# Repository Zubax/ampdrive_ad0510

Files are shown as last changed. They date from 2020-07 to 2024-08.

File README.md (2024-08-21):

# AmpDrive AD0510 / Zubax Komar

Zubax Komar is a high-quality FOC ESC based on [Telega](https://zubax.com/technologies/telega) motor control technology.
Komar is designed to support the propulsion systems of light unmanned aerial vehicles (UAVs), unmanned underwater vehicles (UUVs)
and unmanned surface vehicles (USVs). Komar is compatible with almost all PMSM and BLDC motors.
It is designed to be a part of an integrated drive but allows operation as a separate unit as well.
Komar is one of the reference designs for the [Mitochondrik LV](https://zubax.com/products/mitochondrik-lv) control module.

<p align="center">
Zubax Komar
</p>

## Brief specs

* 12...51 V input voltage range (4...12S LiCoO<sub>2</sub> battery).
* Up to 2500 W output power (with 12S LiCoO<sub>2</sub> battery).
* Maximum continuous phase current amplitude 100 A.
* A software-controllable 5 V BEC.
* Built-in motor temperature sensor for enhanced self-diagnostics.
* Komar supports a rich set of communication interfaces:
  * Double redundant CAN bus interface.
  * USB Micro-B interface for control, management, and telemetry.
  * Industry-standard RC PWM input.
* Komar is built using highly reliable automotive-grade AEC-Q qualified components.
* Operating device temperature - -40..85 °C.
* Operating humidity - 0..100 %RH (Condensation not permitted).
* Weight - 96.5 g (cables not included).

Due to its superb efficiency, Komar can operate at high power levels using only a very lightweight and compact heatsink to cool the device down.

Komar is designed to be a part of an integrated drive for mid-power motors.
It is best suited for motors with the following specs:

* Continuous power: 2.5 kW
* Continuous phase current amplitude: 90 A
* Outer diameter: 80 mm

Komar can also be used as a separate unit. In this case, a custom phase connector mounted on the housing may be used to provide motor connections.

The parameters of the Aux port are as follows:

* $V_\text{pull}=3.3V$ (defined by Mitochondrik)
* $R_\text{pull}=1200\Omega$ (defined by Mitochondrik)
* $R_\text{io}=200\Omega$ at the Aux connector
* $R_\text{io}=0\Omega$ at the through-hole motor thermistor pin on the PCB (see schematics)

## Construction and usage

Komar itself consists of a power stage PCB with Mitochondrik and the housing (aluminum enclosure plus several plastic parts).
The PCB may use several optional 3D-printed parts that don't influence its properties directly, but may improve the overall user experience:

- Lightpipe
- Capacitor support

## Connections and indication

All connections (except the phase connector) and indicators are presented on the bottom cover, as shown in figure below.

Komar connectors and LEDs placement

Pinout of connectors is presented in the tables below. 

### CAN1 & CAN2 connectors (type JST BM04B-GHS)

| Pin # | Type  | Name  | Comments |
|---|---|---|---|
| 1 | Power | PWR | BEC 5V power output. Activated in the firmware. |
| 2 | I/O | CAN_H | |
| 3 | I/O | CAN_L | |
| 4 | Power | GND | |

The device does not terminate the CAN bus internally.
If the bus is not redundant, only CAN1 (the primary CAN bus interface) can be used.

### AUX connector (type JST BM04B-GHS)

| Pin # | Type  | Name  | Comments |
|---|---|---|---|
| 1 | Power | PWR | 5V line output |
| 2 | I/O | GPIO1 | GPIO/RCPWM input/Thermistor input |
| 3 | I/O | GPIO2 | |
| 4 | Power | GND | |

The motor windings temperature can be measured by means of a PTC thermistor. The following thermistors can be connected between GPIO1 and GND:

- KTY84/130
- KTY81/120
- KTY83/120

No additional components are needed for the thermistor. The thermistor model is selected in the firmware.

### USB connector

Common USB 2.0 Micro-USB connector is dedicated for the device configuration and control using the [Kucher GUI](https://files.zubax.com/products/com.zubax.kucher/1.0.0/).

## Thermal performance

Thermal simulation is performed under the following conditions:

* The heat source is applied to the heatsink area where the PCB is placed. Its power is 78.5 W.
  It is a typical value of power losses in the Komar power stage when operating at a power level of 2500 W
  and powered from a discharged 12S battery (~40 V). This should represent the worst-case scenario.

* Ambient temperature is 20 °C.

* The convection value of 350 W/(m<sup>2</sup>K) is established empirically after conducting several experiments with real hardware.

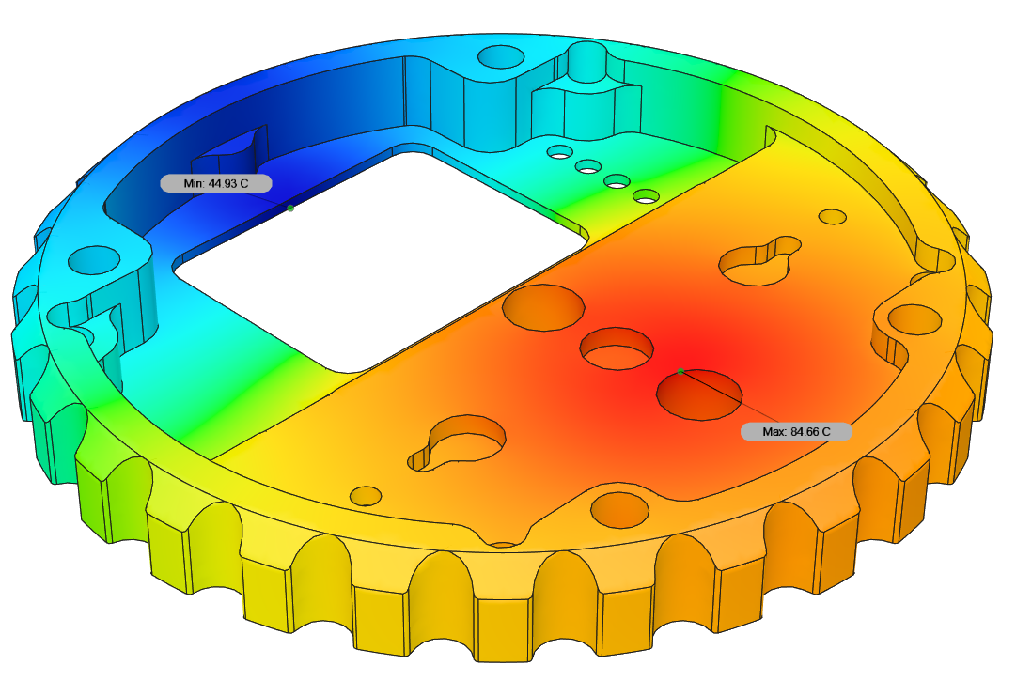
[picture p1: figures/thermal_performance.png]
Zubax Komar thermal performance


## Mounting pattern

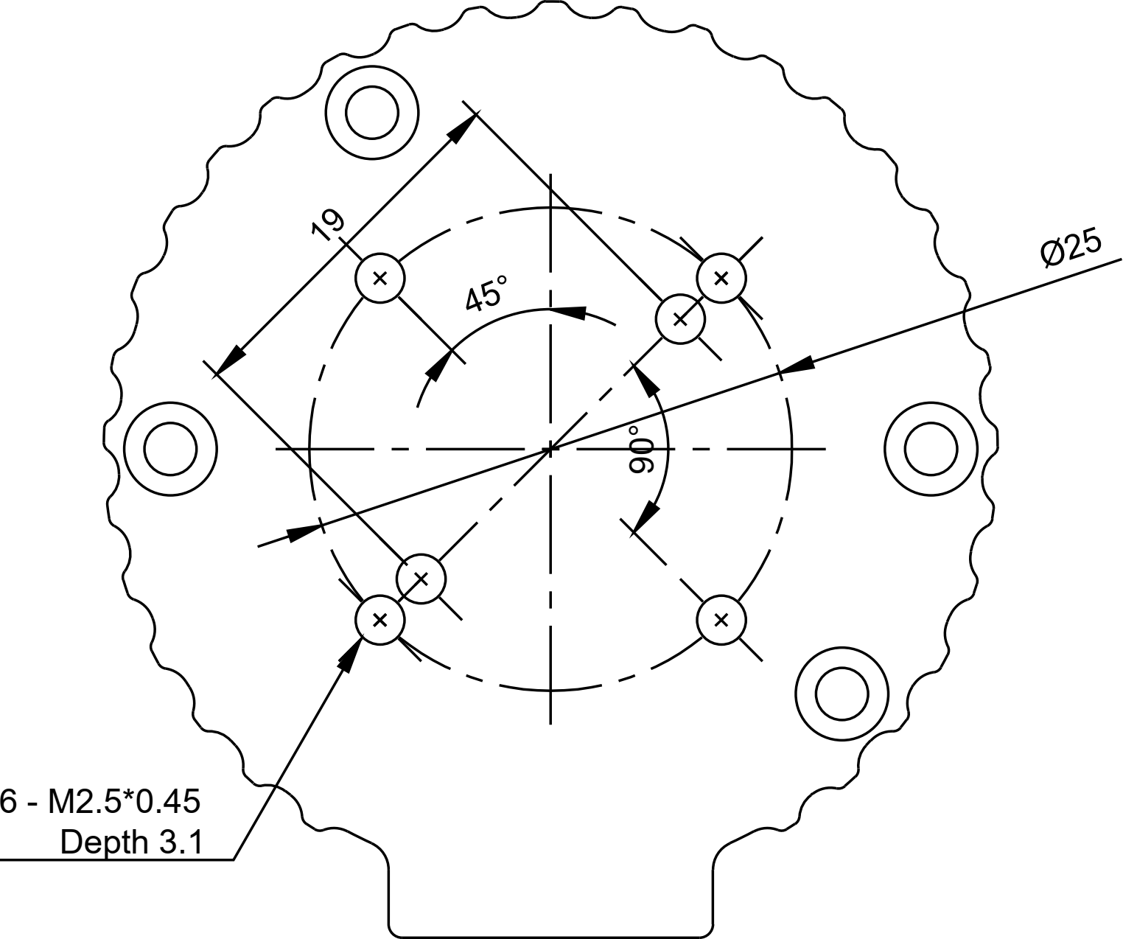
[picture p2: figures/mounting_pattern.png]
Zubax Komar mounting pattern


## VSI Configuration

All Komars with Telega v1 (Cyphal) are configured with the following VSI parameters by default.

```
sys.golden:               sys. vsi.
vsi.bridge_resistance:    [0.002, 0.003, 0.002, 0.003, 0.002, 0.002]
vsi.phase_current_gain:   [100, 100,  25,  25]
vsi.phase_current_stderr: [0.3, 0.3, 0.2, 0.2]
vsi.thermistor_v2k:       [223.15, 100.0, 0.0]
```

Please refer to the manufacturing manual and schematics for further information.
The most up-to-date documentation is attached to the latest published
[release package](https://github.com/Zubax/Komar/releases).

## Release notes

Newest entries at the top.

### Komar v1.6 (work in progress)

* The USB connector will no longer be installed, as USB is not supported in Telega v1.
* to be continued...

### Komar v1.5 (January 2023)

* Updated alternative for MCP9700AT-E/TTVAO to MCP9700T-E/TT.

### Komar v1.4 (January 2023)

* Removed alternative for Diode BAV99HDWQ-13.
* Increased the hardware over-current protection trip level to 427A.

### Komar v1.3 (November 2022)

* Changed DC/Battery power wire to 12 AWG in the assembly manual.
* Corrected Micro USB attributes in the schematic.
* Added alternative parts:

| Part | Alternative | Function |
| ---| ---| ---|
| ATA6561-GBQW-N | TJA1441DTK/0Z | CAN TRANSCEIVER |
| FDMS86368-F085 | BSC080N12LSGATMA1 | FET |
| BAV99HDWQ-13 | BAV70HDWQ-13 | DIODE |
| MCP9700AT-E/TTVAO  | MCP9701T-E/TT | THERMISTOR |
| ELXZ630ELL331MK20S | EEU-FC1J331B | CAPACITOR |
| NRVB120VLSFT1G | NRVB230LSFT1G | DIODE |

### Komar v1.2 (July 2021)

* USB connector with mounting pads swaped with through-hole USB connector to ensure durability.
* Manufacturing instructions update.
* New design of the phase connector.
* Phase connector manufacturing instructions and jig added.
* A better design of the PCB spacer added.

### Komar v1.1 (August 2020)

* Panel template fix: solder mask issue with phase connectors pads fixed (#13).
* Enclosure: increase chamfering depth (#14).

### Komar v1.0 (July 2020)

#### Major PCB updates

* All components are AEC-Q qualified to be compatible with the hardware design policies.
* Better and bigger bulk capacitors.
* Holes for adding 3D-printed capacitor supports added; capacitor supports  developed (not shown on the PCB).
* All the gate networks re-routed and greatly improved.
* All the LEDs grouped in one place; holes for mounting lightpipe added.
* Holes diameter for power supply wires soldering greatly increased to fit any 3.3 sqmm multi-stand wire.
* Holes diameter for phase wires increased to fit either any 2 sqmm multi-stand wire
  (in the case of motor soldering to the PCB) or 3.3 sqmm single-strand wire (if phase connectors are used).
* Overcurrent protection trip level increased 1.5 times to theoretical value of 200 A.
  In practice, however, the overcurrent protection tends to trip at approx. 20-30% below the configured level
  due to the temperature drift of the MOSFETs R<sub>DS(on)</sub> and RF noise.
* TVS diodes with a lower reverse standoff voltage are used (51 V).

#### Major housing changes

* The housing parts are now held together with 4 M3.5 screws instead of M3.
* The housing itself is now mounted on the chassis using 4x M4 screws (was M3).
* Wall thickness of the top part of the housing increased from 1 to 1.6 mm.
* The connector window is slightly smaller now.
* A totally different construction of the phase connector.
  It is much bigger and accepts bullet connectors up to 6 mm (previously, 3.5 mm bullet connectors were used).
* Phase connector is now supposed to use single-stranded thick stiff copper wires instead of flexible multi-stranded ones.
* All the LEDs are grouped in one place now. The holes for the LEDs have been moved.
* Lightpipe for the LEDs added (will be manufactured inhouse using 3d printing).
* 3D-printed spacers between the PCB and the housing added.
* Slightly improved the heatsink efficiency by redesigning the fins.
* 3x M2.5 holes for mounting optional (and not yet developed) connector protection cap added.
* Optional power connector assembly  mount added.

### Komar v0.2 (2018)

First release that was actually manufactured.

### License

This project is licensed under the terms of [CC-BY 4.0](https://creativecommons.org/licenses/by/4.0/).

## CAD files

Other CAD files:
rigid phase connector jig.f3z

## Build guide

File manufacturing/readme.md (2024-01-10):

# Zubax Komar power stage manufacturing instructions

The manufacturing documentation package contains the following entities:

* Gerber files.
* Assembly drawings (in PDF format) and centroid files.
* BOM spreadsheet.
* PCB stack specification exported from the EDA.
* This document.
* Manufacturing documentation for the sub-assemblies:
  * Rigid phase connector assembly.

## Components

### PCB

The PCB is 4-layer with 35 um copper on all layers.
Its dimensions is a circle with a diameter of 58 mm.
The total PCB thickness is 1.6±0.1 mm.
The solder mask color should be red, silkscreen color -- white.

The copper layers are ordered as follows:

1. copper_top_l1
2. copper_inner_l2
3. copper_inner_l3
4. copper_bottom_l4

### Plastic part

One custom 3D-printed plastic part is needed for the assembly: motor phase wires interface.

It can be printed using a generic FDM 3D printer using ABS filament.
The recommended settings are as follows:

* Nozzle diameter: 0.3-0.4 mm
* Layer width: 0.36-0.44 mm
* Layer height: 0.1 mm

### Thermal pad

The thermal pad serves as thermal interface between the PCB and the housing.
The thermal pad has a relatively complex shape, some kind of jig may be used to cut it in a repeatedly and easy way.
Use the picture below as a reference.
The detailed thermal pad drawing can be exported from the 3D model of the device.



### PCB spacer

The PCB spacer is a flat part that is placed between the main PCB and the bottom part of the housing to provide proper distance between them.
It also protects the main PCB from damaging it with mounting screws in case their length is incorrectly selected.
It can be laser cut from any sheet material with 0.5 mm thickness that can withstand temperature up to 100 °C. 
It can also be manufacted as a general PCB with all copper removed. In this case the main criteria is thickness.
Most PCB houses offer cheap manufacturing of PCBs with thickness of the resulting PCB down to 0.6 mm. 
Substracting 2 copper layers of 0.35 mm each, the resulting PCB can have ideal thickness of 0.53 mm which is suitable. 

Exact drawing of this part for laser cutting can be exported from file **pcb spacer.brd** in the root of this repository.

### Bill of materials

PCB assembly not included. Solder and consumables not included.

Item                          | Amount| Part number                                                     | Description
------------------------------|-------|-----------------------------------------------------------------|-------------------------------------------------------
Silicone glue                 | ~3 ml | Penosil 2121                                                    | Used for fixing two bulk aluminum capacitors.
Conformal coating             | ~3 ml | Taerosol PRF 202                                                | Fast-curing protective coating.
Rigid phase connector         | 0/1   | (see enclosed assembly documentation)                           | 3D-printed. Used with **option #1 motor phase wires interface.**
Phase wires inlet             | 0/1   |                                                                 | 3D-printed. Used with **option #2 motor phase wires interface.**
Positive wire                 | 1     | Copper 12 AWG multi-strand silicone/PVC red 105 °C              | Positive power wire. Total length 200 mm. Remove insulation and tin at both ends 5 mm.
Negative wire                 | 1     | Copper 12 AWG multi-strand silicone/PVC black 105 °C            | Negative power wire. Total length 200 mm. Remove insulation and tin at both ends 5 mm.
Housing top                   | 1     |                                                                 | Milled from aluminum.
Housing bottom                | 1     |                                                                 | Milled from aluminum.
Housing screw                 | 4     | DIN 965 M3.5 16 mm                                              | Fastening both parts of the housing together.
PCB spacer                    | 1     |                                                                 | Flat part that lifts the main PCB from the heatsink. 
Thermal pad                   | 60x30 mm | Arctic Cooling ACTPD00018A, ACTPD00005A, or ACTPD00002A      | Sinks the heat to the bottom part of the housing.

## Assembly

### 1. SMD assembly

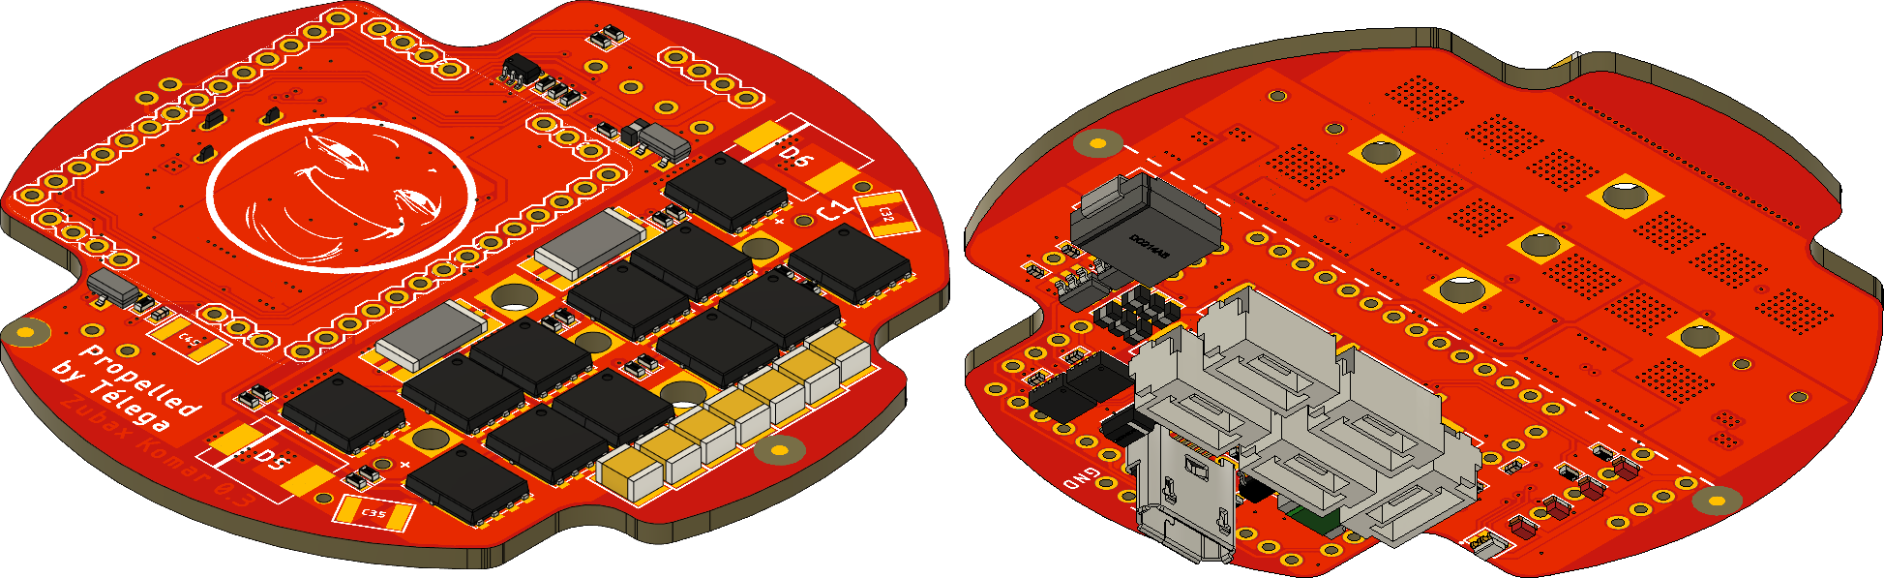
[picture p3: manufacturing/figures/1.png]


### 2. Mitochondrik mounting

Prior to mounting the Mitochondrik,
the PLS2 pin headers (CON100, CON101, CON102, CON103, CON104, CON105) should be soldered to the PCB.
The Mitochondrik is inserted on top of these headers and soldered.

### 3. Capacitor soldering

The C1 and C2 radial electrolytic caps should be soldered sideways as shown in the picture below.
Ensure the correct polarity.

The capacitors should be glued to the PCB with a non-conductive silicone glue
(see the BOM table for the recommended partnumber).

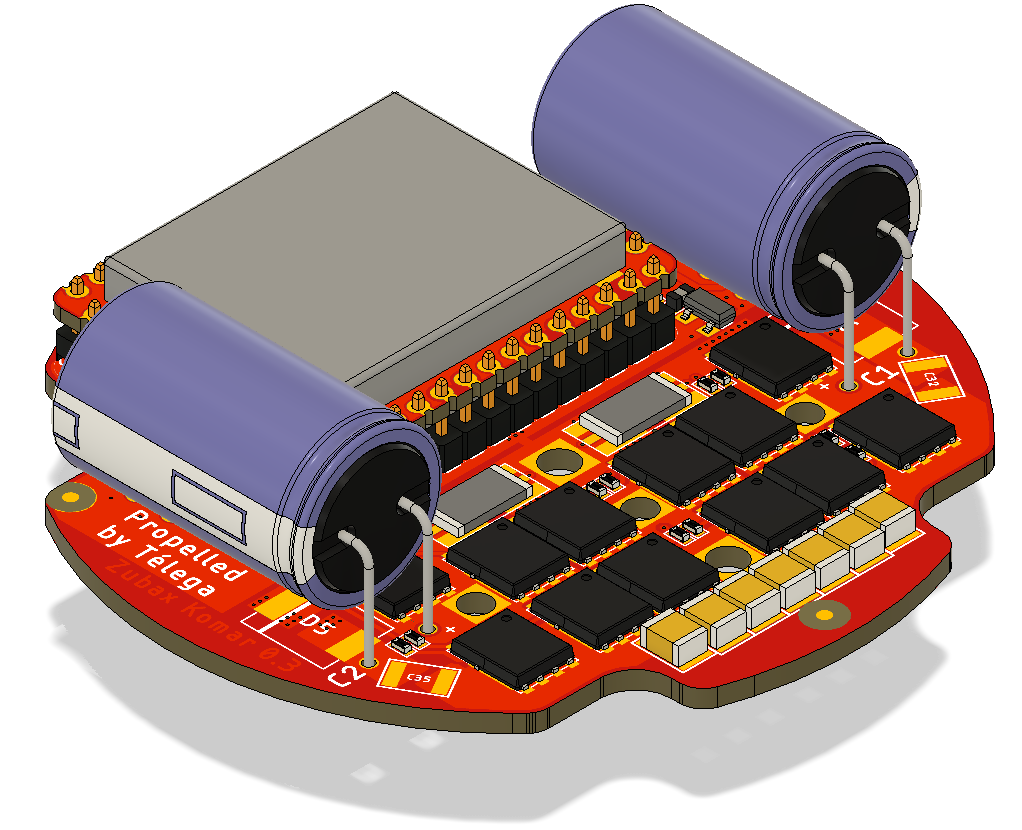
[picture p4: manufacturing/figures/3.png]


### 4. Power wires soldering

The ends that are not soldered to the PCB should be stripped and tinned (approx. 5 mm).
The wires should be soldered as shown in the pictures below.

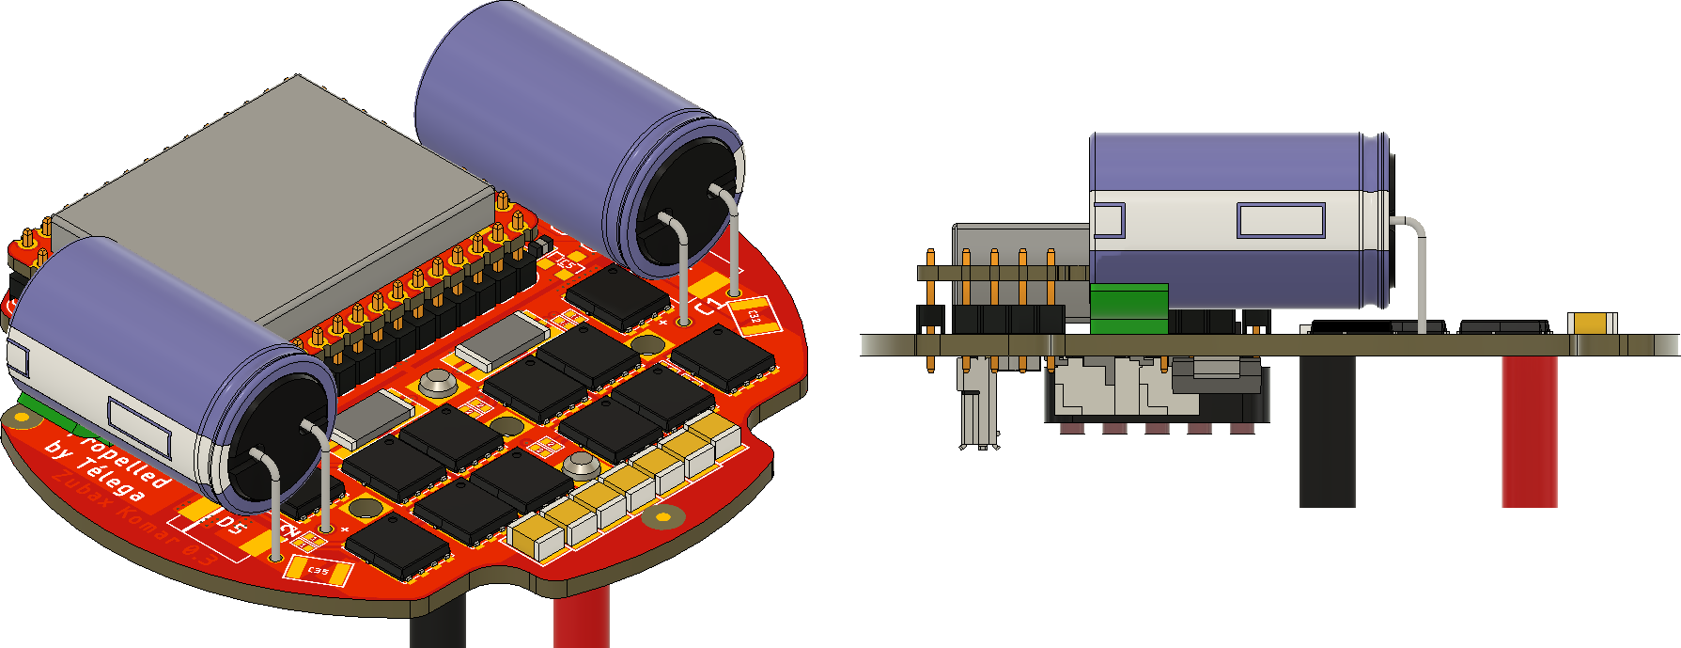
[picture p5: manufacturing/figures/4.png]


### 5. Motor phase interface assembly

The motor phase interface can be assembled in one of the configurations described in this section.

#### Option #1. Rigid phase connector

The phase connector is shown in the picture below.
The guide for low-volume production is available in the adjacent document.

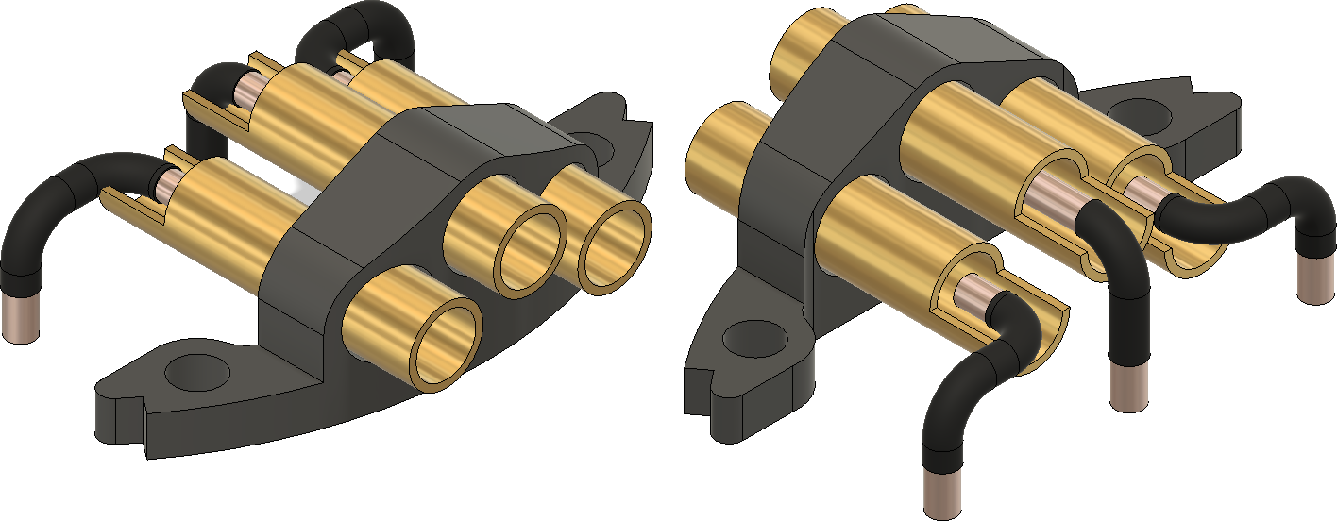
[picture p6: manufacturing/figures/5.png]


It should be soldered to the PCB so that the bottom surface of the plastic part rests on the PCB:

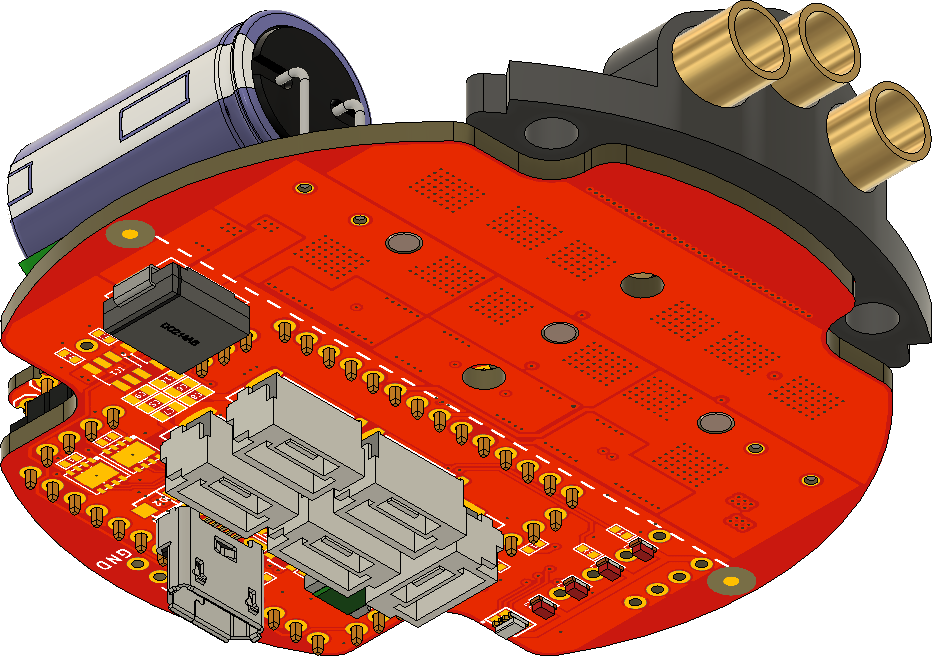
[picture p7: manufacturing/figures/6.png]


#### Option #2. Fixed motor attachment

The motor is installed onto the top part of the enclosure.

The motor phase wires are routed inside the enclosure through a 3D printed cable inlet, cut to the appropriate length,
and then soldered to the PCB.
The cable inlet can be seen on the picture below.
It is fixed on the top part of the housing in a similar way to the rigid phase connector.
Minor modifications of the cable inlet may be necessary depending on the particular motor phase wires' thickness.

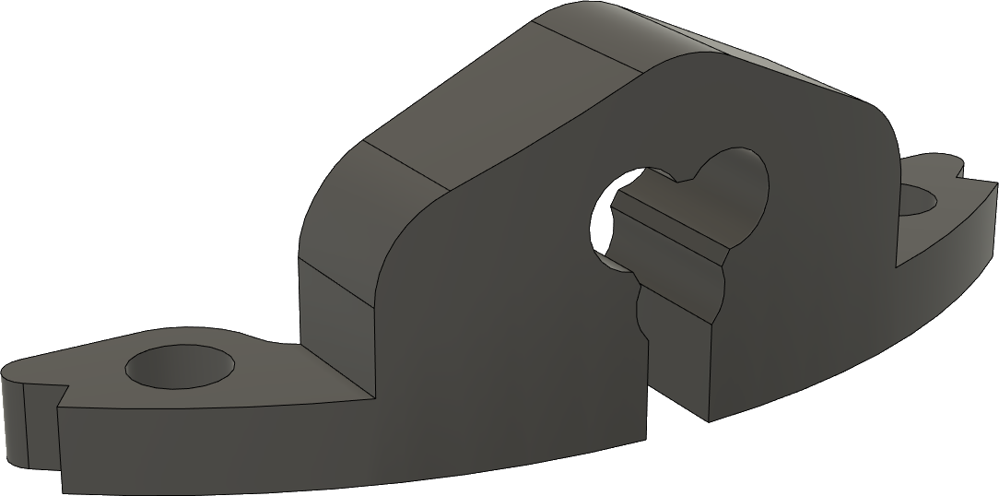
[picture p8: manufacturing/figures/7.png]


The motor and its parts, if any, are not part of the bill of materials.

### 6. Conformal coating

The PCB should be conformal-coated (see the BOM table for the recommended partnumber),
excluding the connectors on the bottom side of the PCB (CON1, CON3, CON4, CON5, CON6, CON7)
and the inner surfaces of the phase connectors.

### 7. Housing assembly

The blow scheme for motor phase interface option #1 (rigid phase connector) is shown in the picture below.

Komar blow scheme with a rigid phase connector

#### Bottom part assembly

Insert the **thermal pad** and the **PCB spacer** into the bottom part of the housing as shown in the picture below.

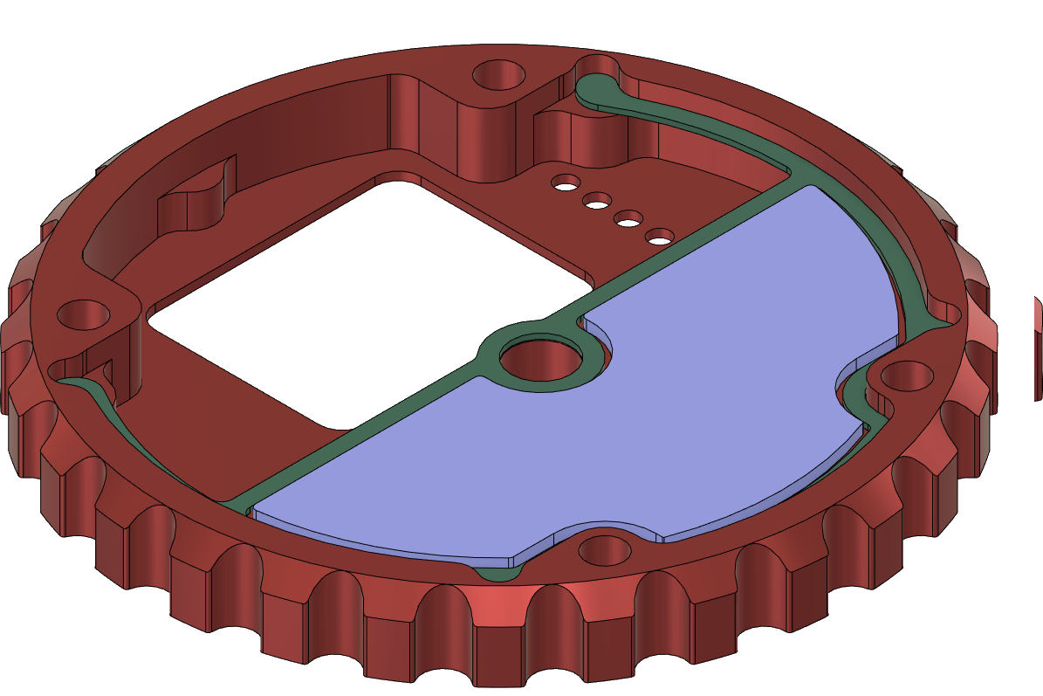
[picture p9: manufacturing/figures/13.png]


After that, the **PCB assembly** can be installed on top of the **thermal pad**.
The **positive wire** and **negative wire** should run through the corresponding holes in the housing.

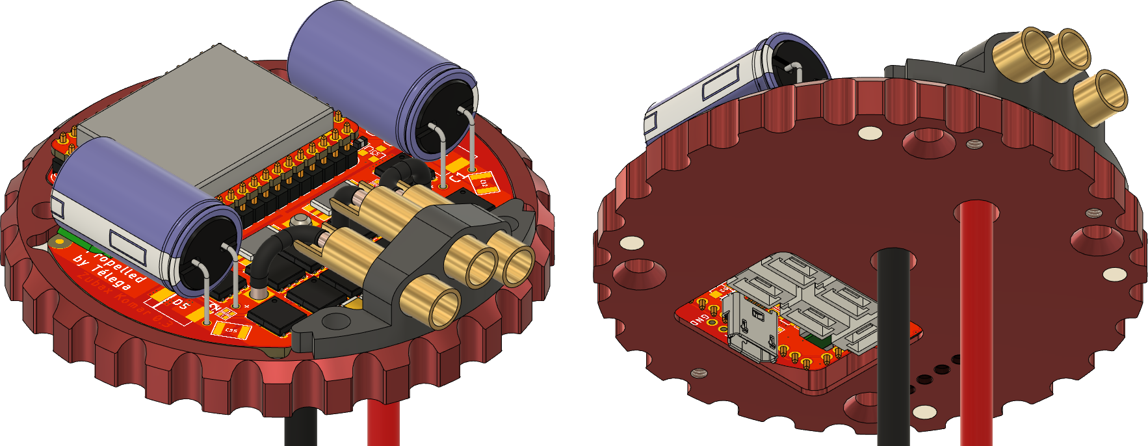
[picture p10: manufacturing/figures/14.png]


#### Top part assembly

If needed, the motor should be installed on the top part of the housing.
The motor itself and its fasteners are not part of this design.

#### Final assembly

Two parts of the housing should be connected together at this step.
The mounting holes should be aligned and fastened using the set of **housing screws**.

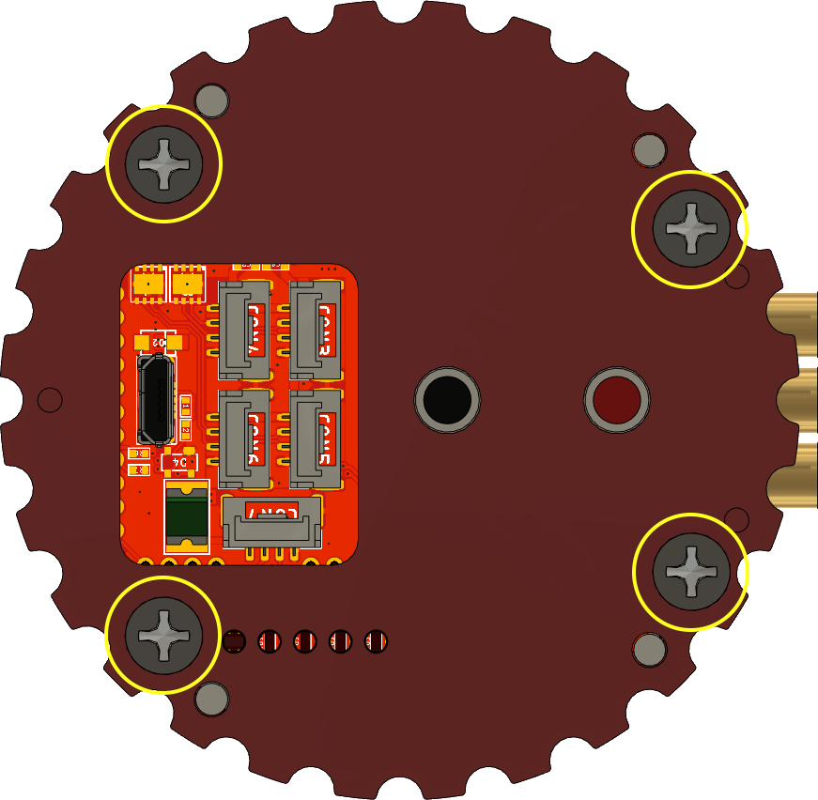
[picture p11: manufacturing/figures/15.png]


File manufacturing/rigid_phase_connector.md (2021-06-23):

# Rigid phase connector

This is the manufacturing documentation for the rigid phase connector sub-assembly.

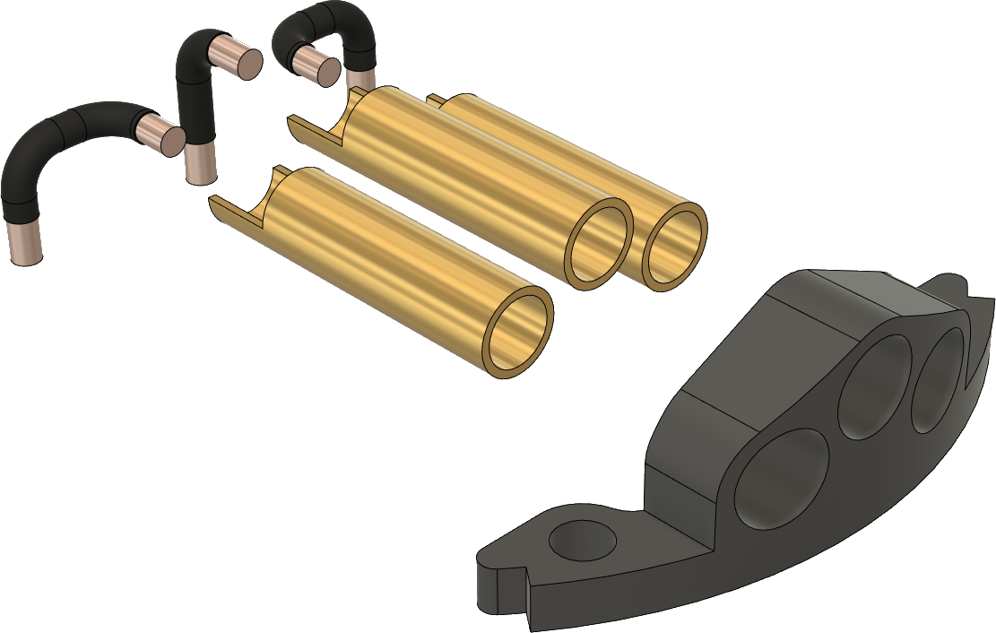
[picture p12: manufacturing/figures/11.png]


A special jig may be used to ease the process of manufacturing. 
The jig consists of two 3d-printed parts that are fastened together using two M3 x 30 mm screws.
The jig allows for precision connector's pins forming and installing 
the bullet connectors into the connector housing at the right depth.

## Bill of materials

Solder and consumables not included.

Item               | Amount | Description
-------------------|--------|-------------------------------------------------------------
Connector body     | 1      | 3D-printed
Bullet connector   | 3      | 4 mm diameter female bullet connector
Wire               | 3×25 mm| 3 mm<sup>2</sup> solid copper wire
Heat shrink tube   | 3×17 mm| Supplied diameter 1-1.5 mm
Epoxy glue         | ~3 g   | N/A

## Assembly

1. 3D print  the connector housing.
   Any generic FDM 3D-printer will do the job.
   No special settings needed.
   Support structures are optional.
   It may be needed to clear the holes for the bullet connectors with a 4 mm drill bit after the printing.

2. Solder the three pieces of wire to the bullet connectors.

3. Form and trim the wires in place using the jig.

3.1 Due to wires' stiffness, it may be hard to form the side wires in place by hand.
To guarantee the wires' proper shape one should use the jig's additional features. 
For setting proper wire length the bullet connector should be pushed against the surface shown red in the picture below.
The wires should be trimmed so they are flush with the jig's bottom surface.

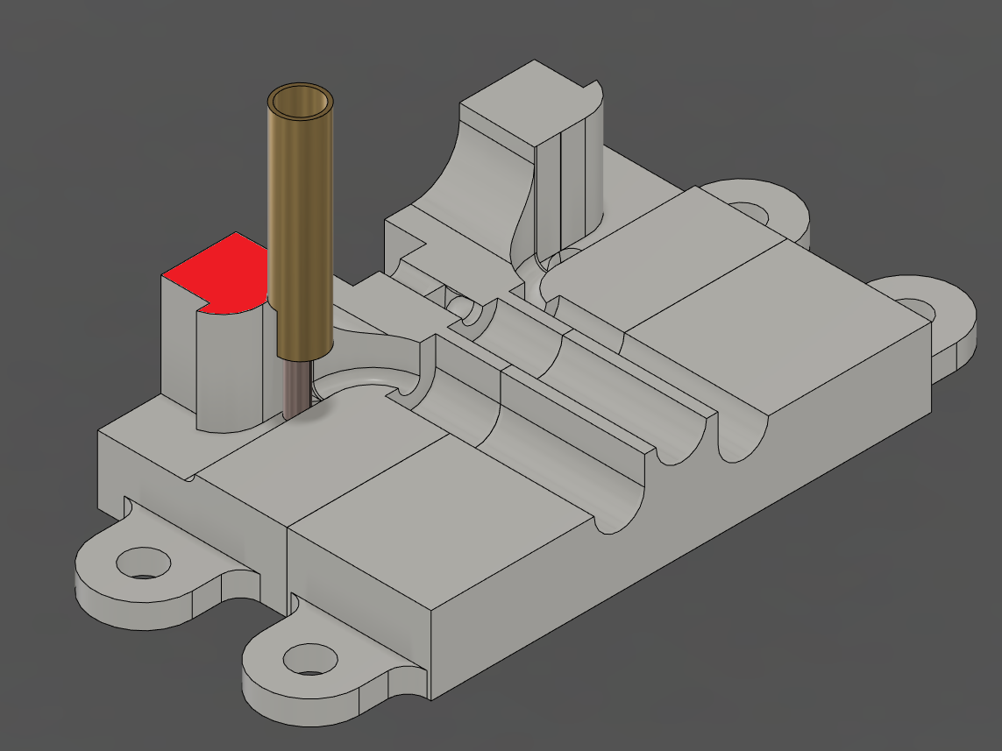
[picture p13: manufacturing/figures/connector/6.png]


3.2. Then while keeping the other end of the wire flush with the bottom of the jig
the side bend can be done in the outer direction of the jig using the rounded surface shown red in the picture below.

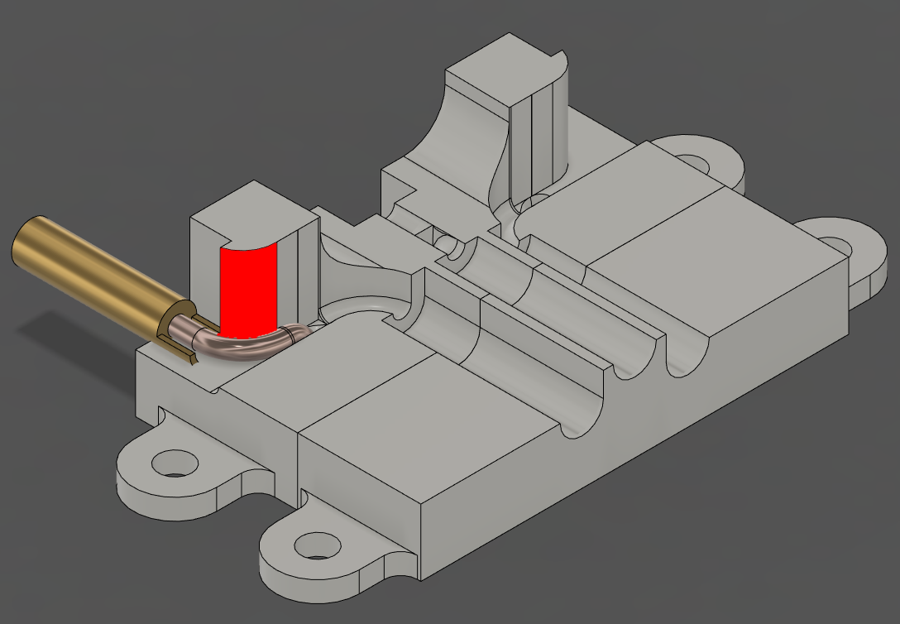
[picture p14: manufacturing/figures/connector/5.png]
 

3.2. Place the bullet connectors with pre-soldered wires into the jig as in the picture below. 

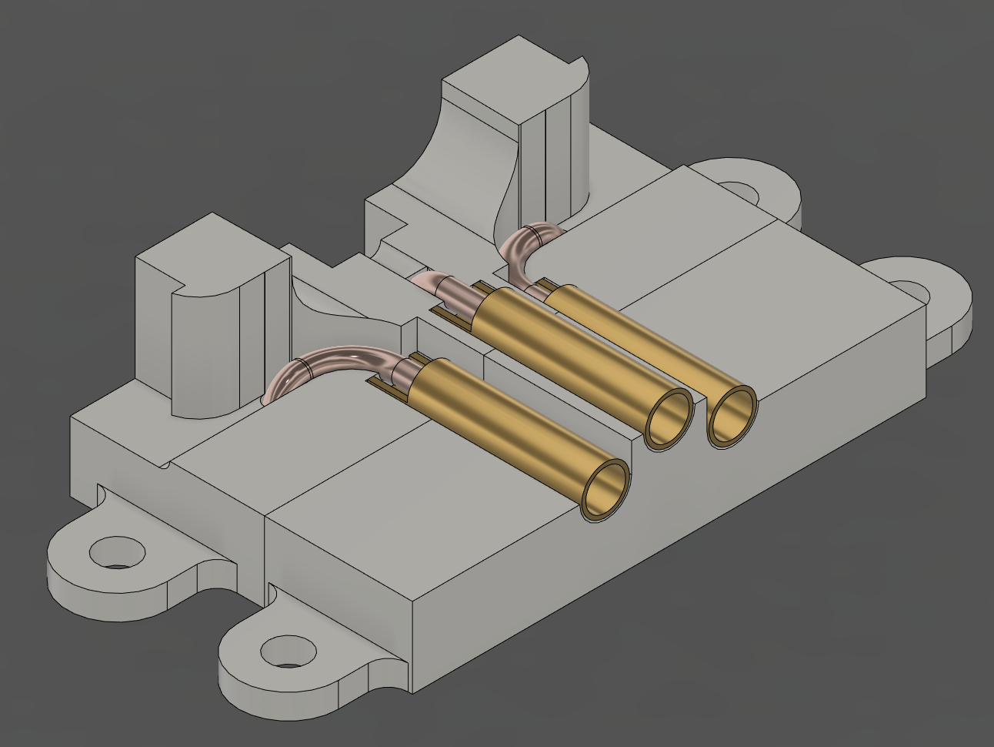
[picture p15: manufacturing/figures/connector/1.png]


3.3. Remove the front part of the jig and the guiding M3 screws.

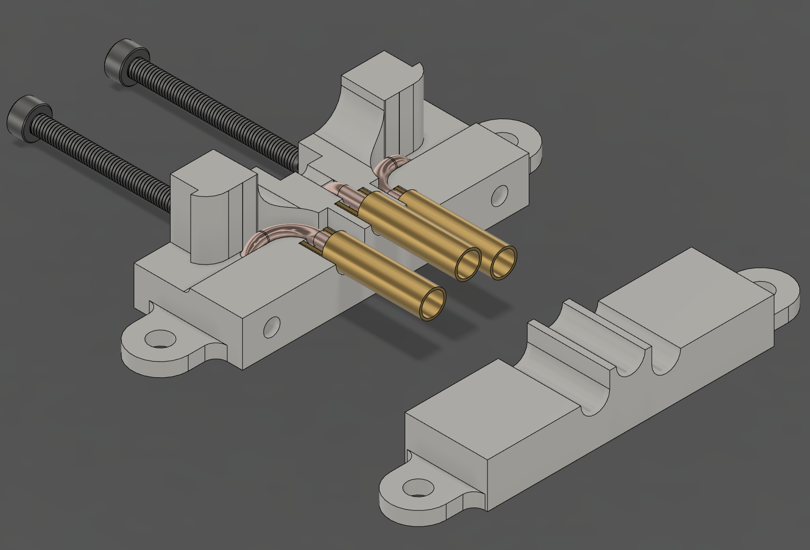
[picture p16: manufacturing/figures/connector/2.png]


4. Apply some epoxy to the bullet connectors and then slip the phase connector housing on the bullet connectors
as far as it can go.

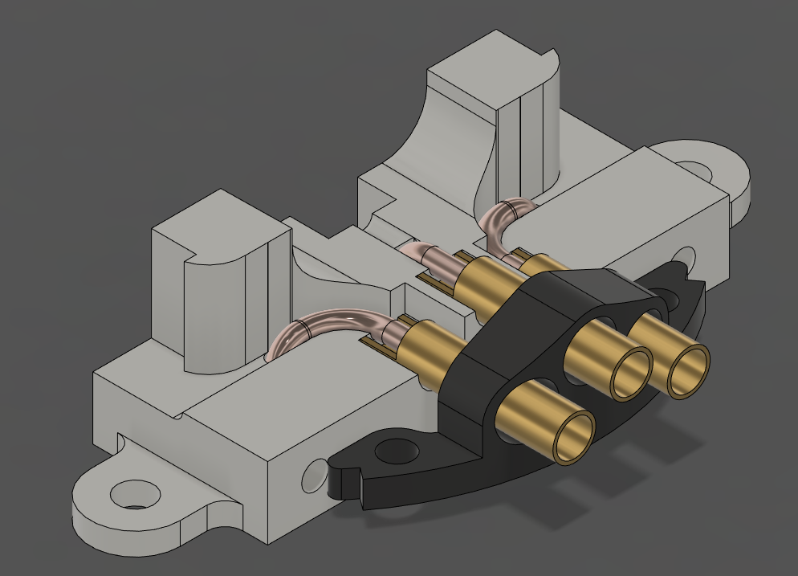
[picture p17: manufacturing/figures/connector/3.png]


5. After the epoxy cures the connector can be removed from the jig by pulling it up.

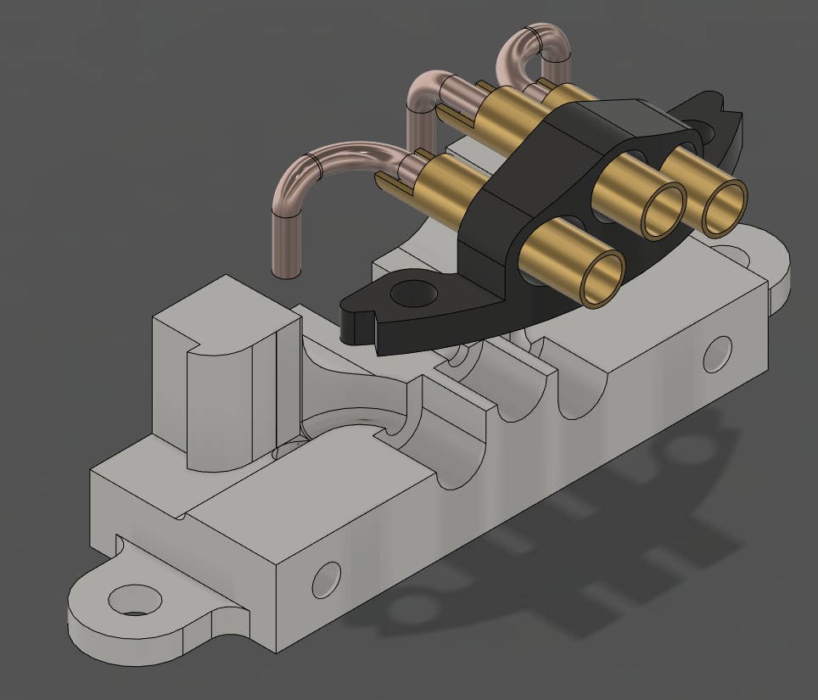
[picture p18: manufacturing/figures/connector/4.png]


6. Place a piece of heat shrink tube on each wire so that it covers all the surface of the wire excluding
   approx. 2-3 mm on the side that is meant for soldering it to the PCB.
   The final result should be like this:



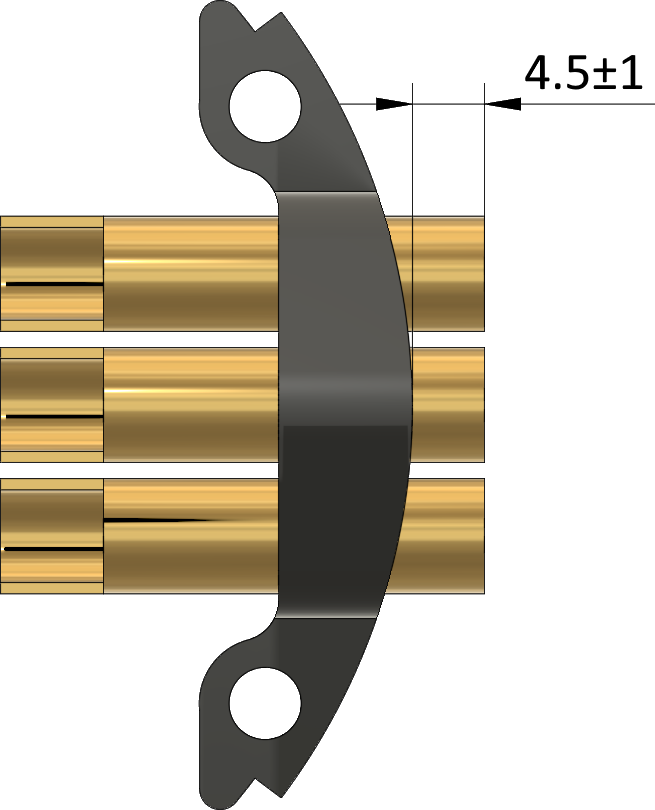
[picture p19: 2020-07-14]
manufacturing/figures/12.png

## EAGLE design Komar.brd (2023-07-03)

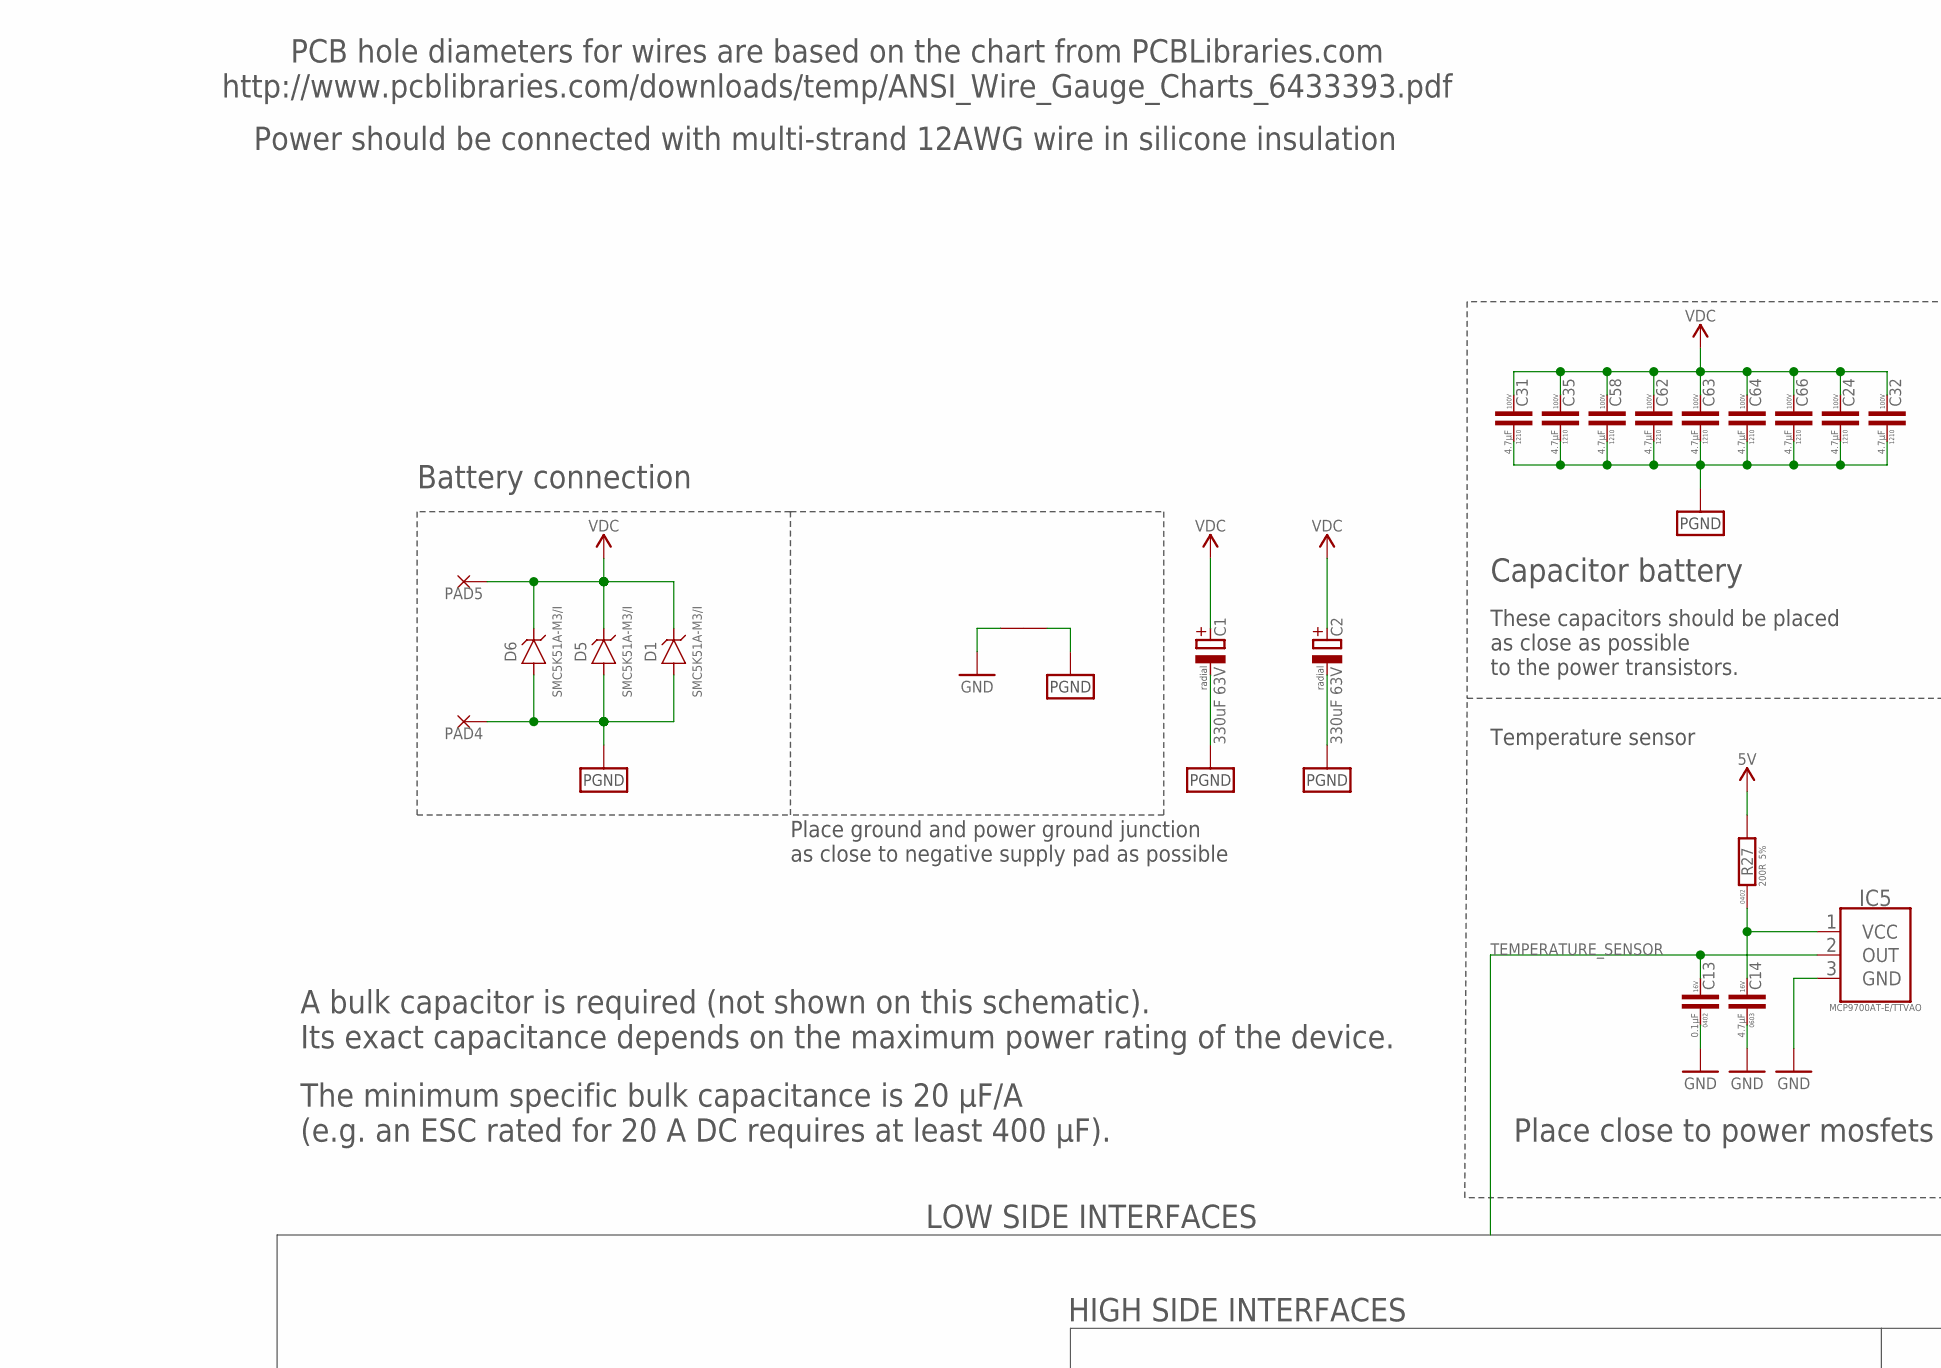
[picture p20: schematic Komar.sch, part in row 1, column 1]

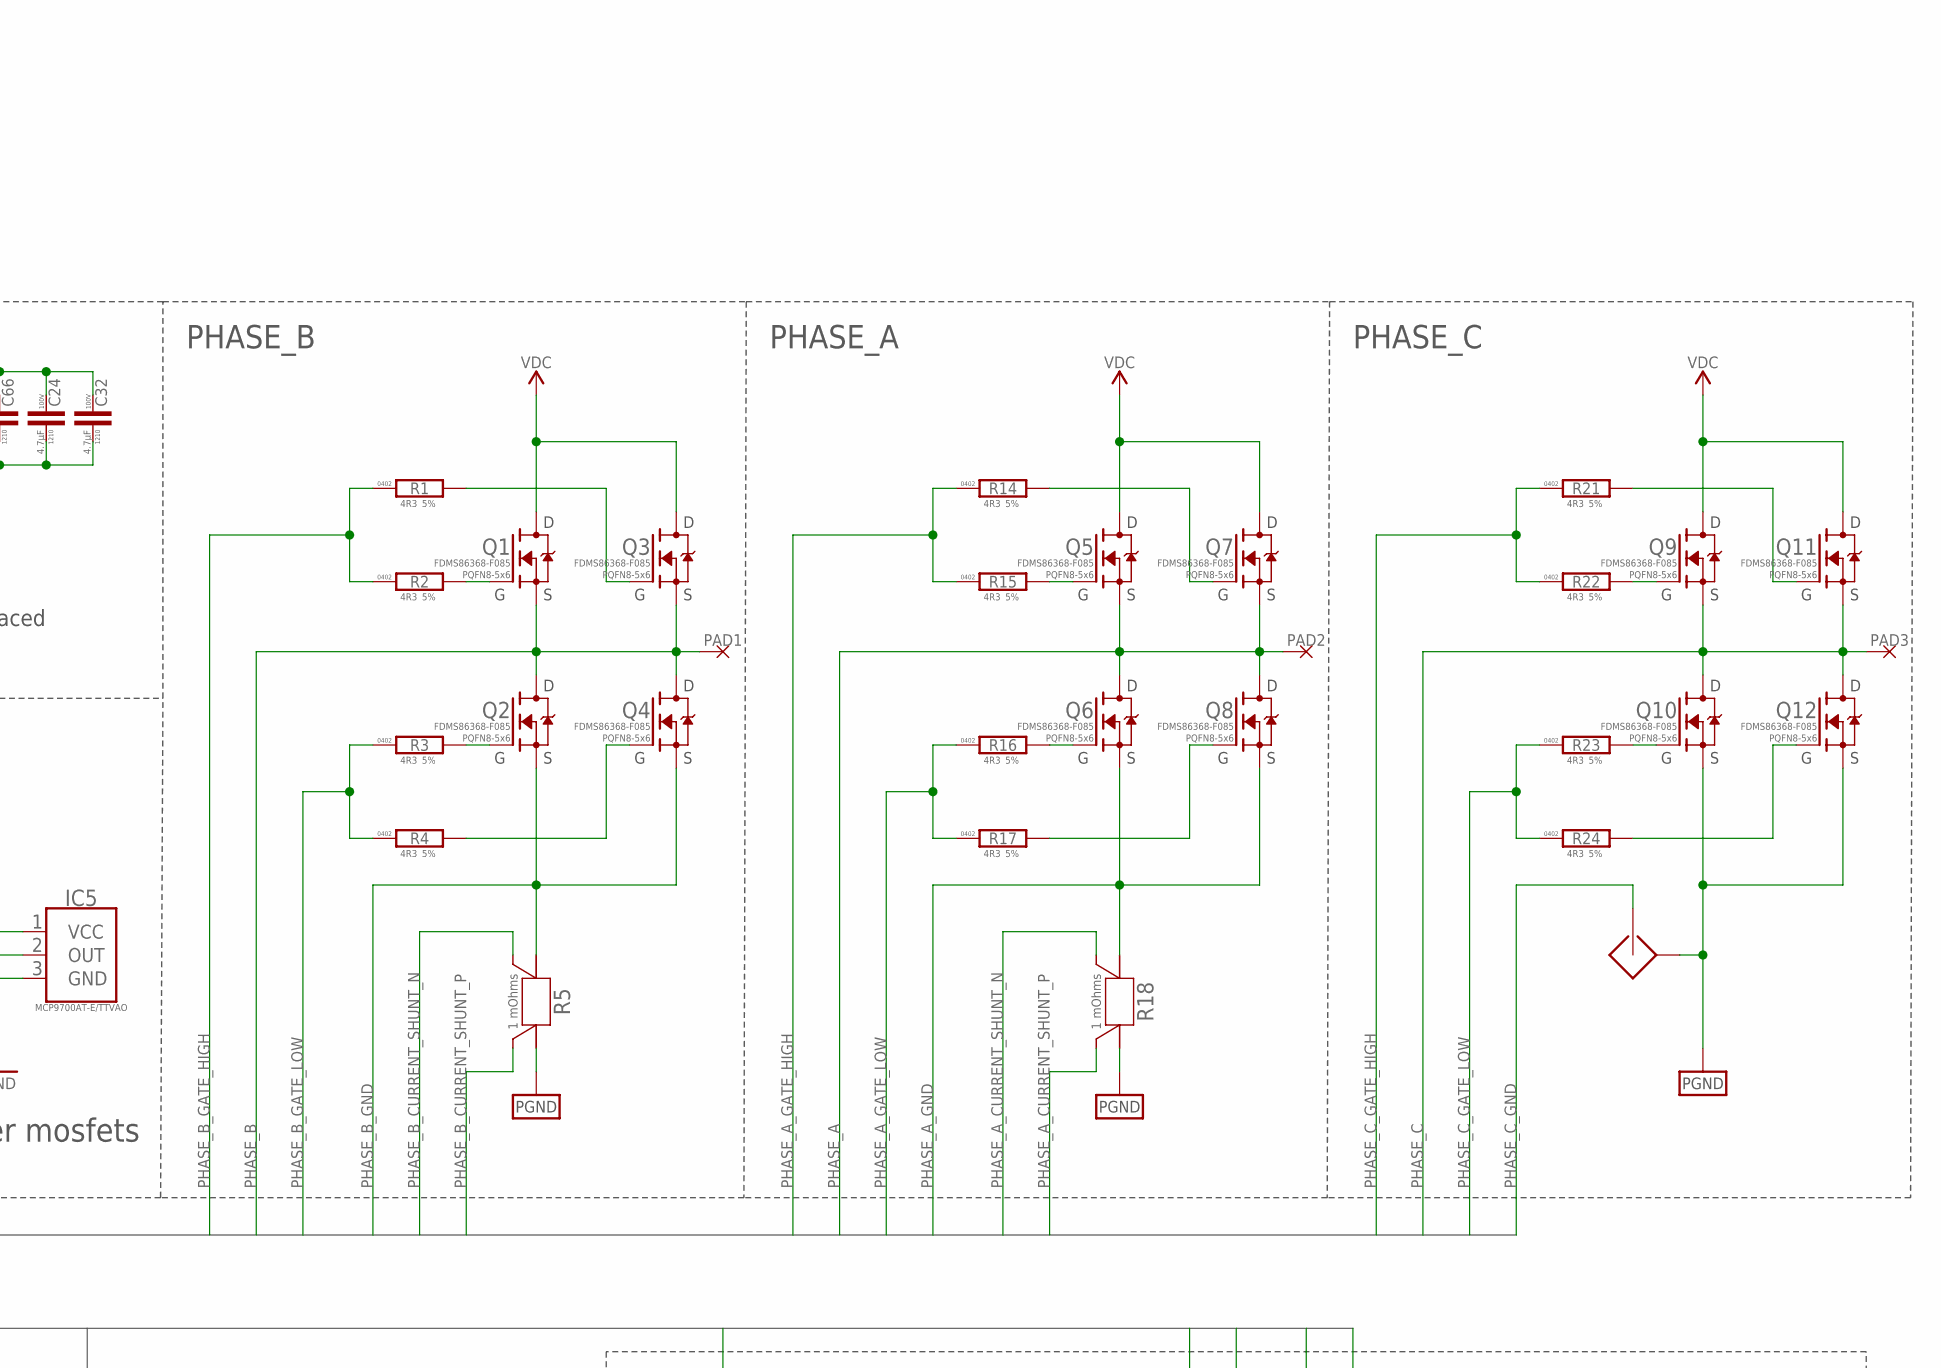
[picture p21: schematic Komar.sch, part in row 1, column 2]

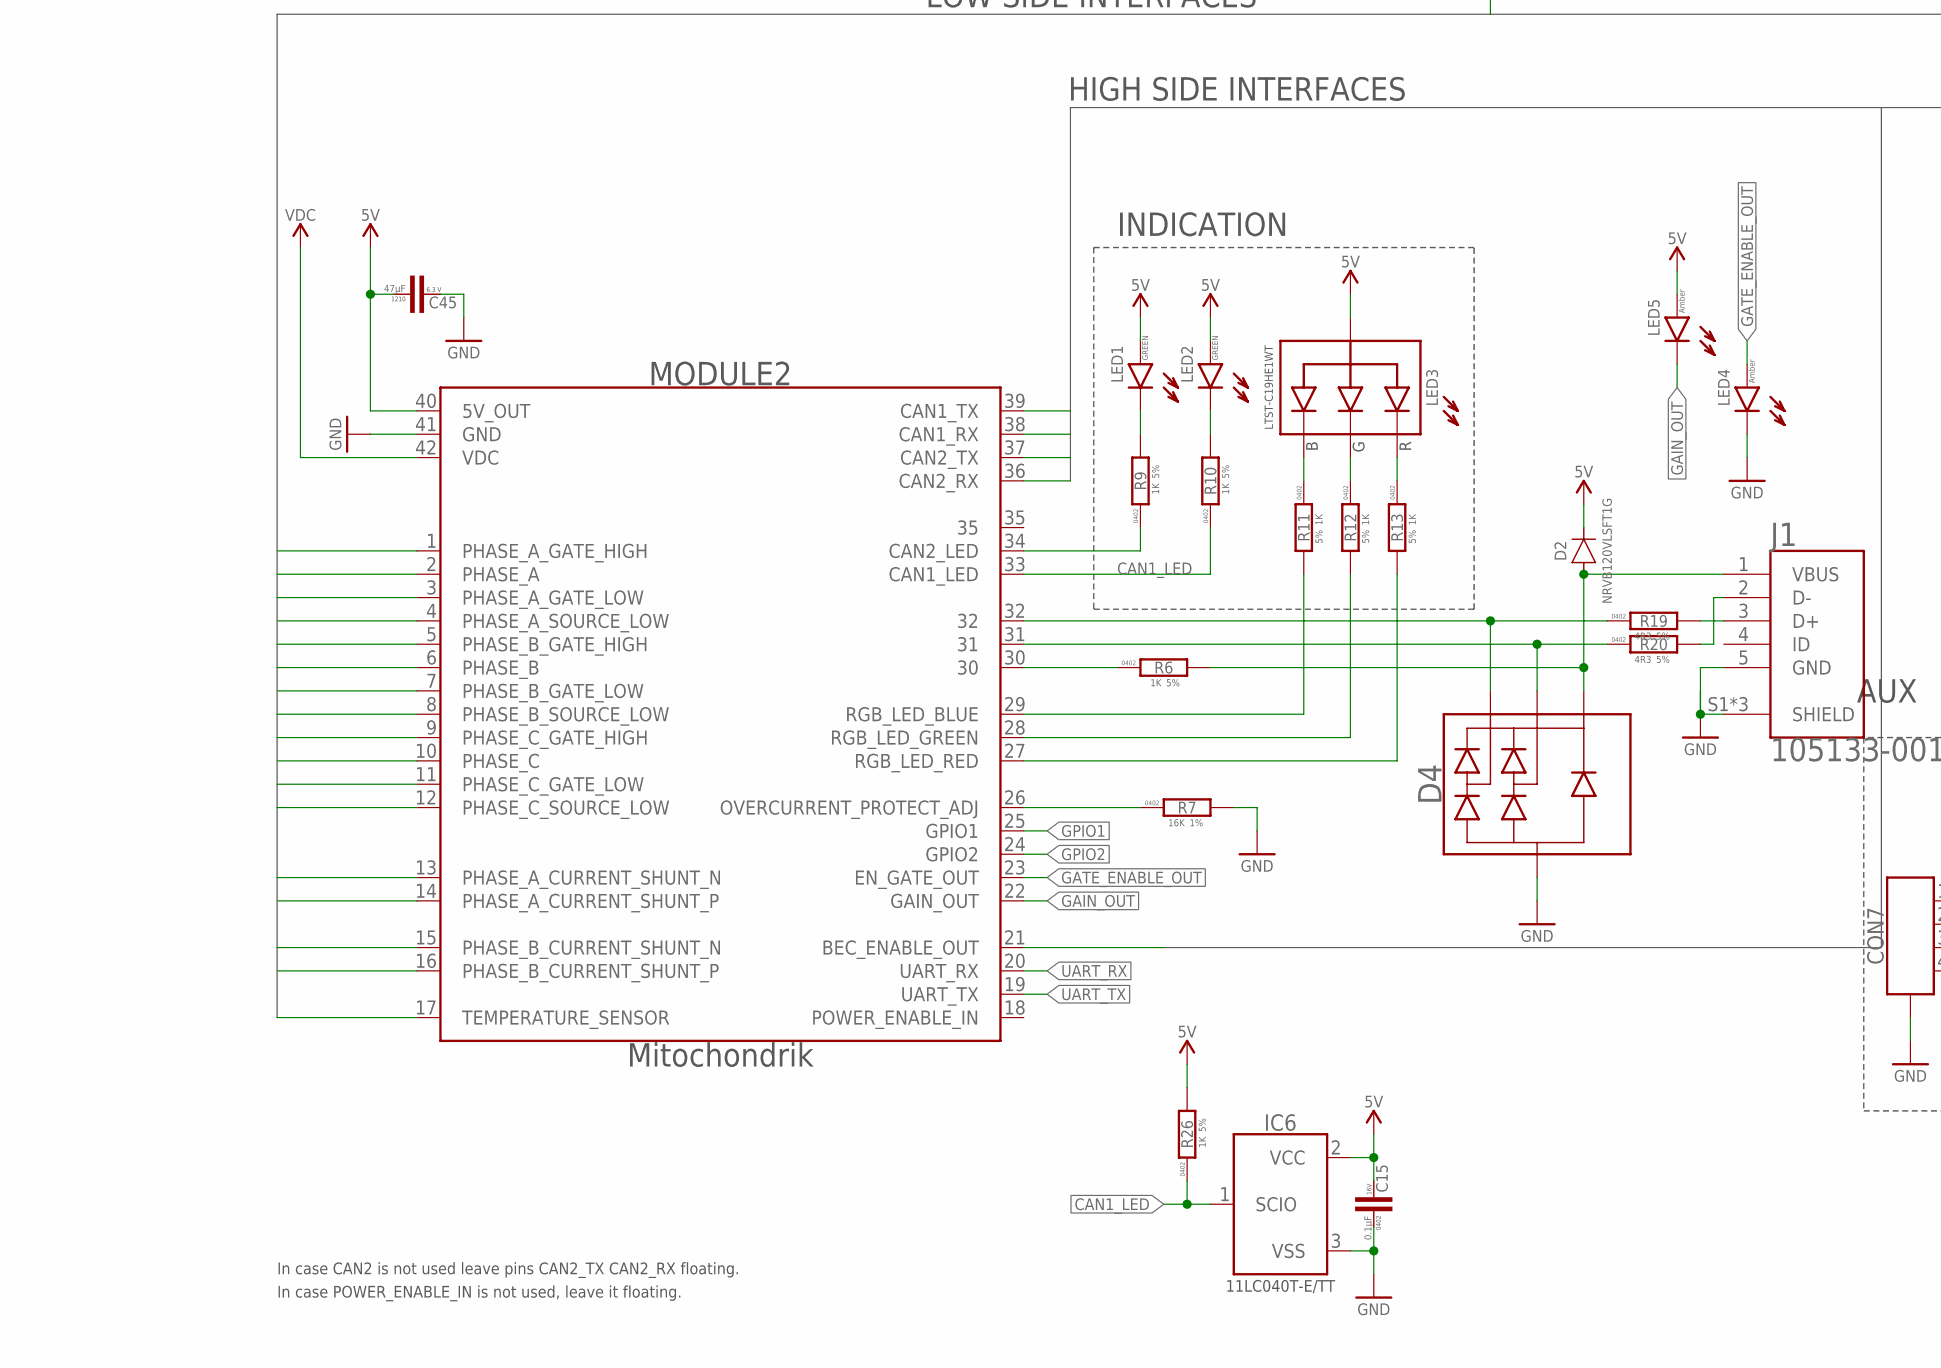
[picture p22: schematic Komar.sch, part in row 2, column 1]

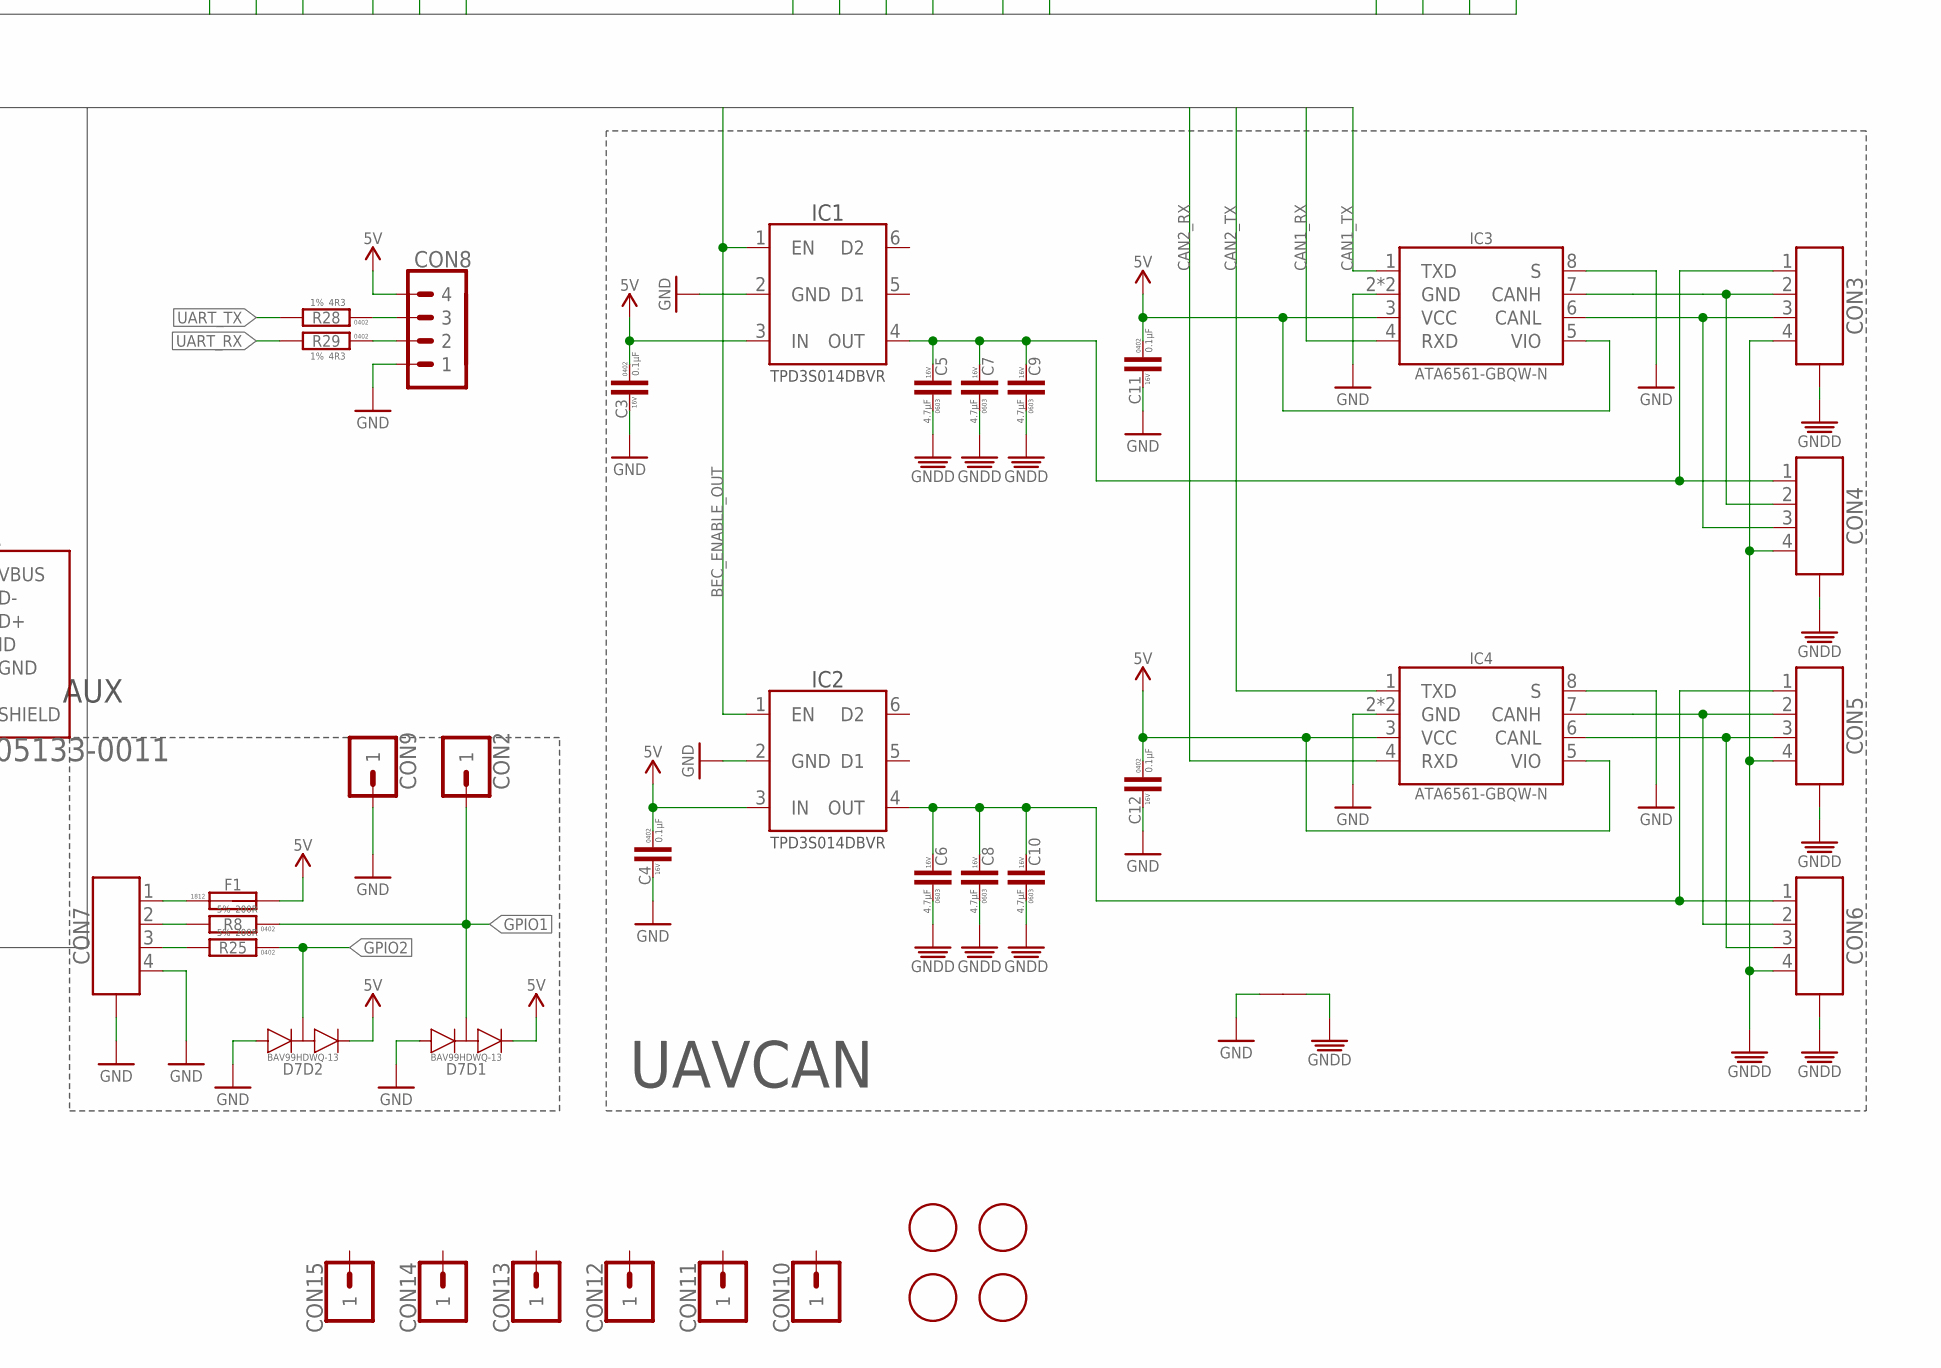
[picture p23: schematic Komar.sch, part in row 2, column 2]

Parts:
C1, C2: 330uF 63V; SIDE_10X22; DIGIKEY# 565-2043-ND
C3, C4, C11, C12, C13, C15: 0.1µF; C0402; VOLTAGE 16V; DIGIKEY# 490-7998-1-ND
C5, C6, C7, C8, C9, C10, C14: 4.7µF; C0603; VOLTAGE 16V; DIGIKEY# 490-12289-1-ND
C24, C31, C32, C35, C58, C62, C63, C64, C66: 4.7µF; C1210; VOLTAGE 100V; DIGIKEY# 490-14484-1-ND
C45: 47µF; C1210; VOLTAGE 6.3 V; DIGIKEY# 490-4844-1-ND
CON2, CON9, CON10, CON11, CON12, CON13, CON14, CON15: PINHEAD_1X01-2; 1X01-PTH-2
CON3, CON4, CON5, CON6, CON7: CON-4P-TABS-STRAIGHT; JST_GH-4P-STRAIGHT
CON8: PINHEAD_1X04-2; 1X04-PTH-2
D1, D5, D6: SMC5K51A-M3/I; DO-214AB(SMC)
D2: NRVB120VLSFT1G; SOD123F
D4: DRTR5V0U2SR-7; SOT143B
D7: BAV99HDWQ-13; SOT363
F1: FUSE-1812; F1812; DIGIKEY# MF-MSMF010-2CT-ND
IC1, IC2: TPD3S014DBVR-SOT23-6; SOT26
IC3, IC4: ATA6561-GBQW-N-HVSON8; SOT782-1
IC5: MCP9700AT-E/TTVAO-SOT23; SOT23B-3
IC6: 11LC040T-E/TT; SOT23B-3
J1: 105133-0011; MOLEX_105133-0011; DIGIKEY# WM10134TR-ND
LED1, LED2: GREEN; LED0402; DIGIKEY# 1830-IN-S42BT5GCT-ND
LED3: LTST-C19HE1WT; 0606
LED4, LED5: ORANGE; LED0402; DIGIKEY# 1830-IN-S42BT5ACT-ND
MODULE2: MITOHONDRIQUE_V0.3-TH; MITOHONDRIQUE-TH
PAD1, PAD2, PAD3: PAD-HOLE_2.4_SQUARE; HOLE_2.4
PAD4, PAD5: PAD-HOLE_2.8_SQUARE; HOLE_2.8
Q1, Q2, Q3, Q4, Q5, Q6, Q7, Q8, Q9, Q10, Q11, Q12: FDMS86368-F085; PQFN8_5X6
R1, R2, R3, R4, R14, R15, R16, R17, R19, R20, R21, R22, R23, R24: 4R3; R0402; DIGIKEY# P4.3JCT-ND
R5, R18: 1 mOhms; R2512-KELVIN; DIGIKEY# CRE2512-FZ-R001E-3CT-ND
R6, R9, R10, R11, R12, R13, R26: 1K; R0402; DIGIKEY# P1.00KLCT-ND
R7: 16K; R0402; DIGIKEY# P124444CT-ND
R8, R25, R27: 200R; R0402; DIGIKEY# P200JCT-ND
R28, R29: 4R3; R0402; DIGIKEY# 2
S1: SENSE; SENSE-0.6
U$1, U$3: CONNECTION-SMD; CONNECTION
U$5, U$6, U$7, U$11: FIDUCIALMOUNT; FIDUCIA-MOUNT

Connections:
AGH1: Q7.4 (G), R14.2
AGH2: Q5.4 (G), R15.2
AGL1: Q8.4 (G), R17.2
AGL2: Q6.4 (G), R16.2
BEC_ENABLE_OUT: IC1.1 (EN), IC2.1 (EN), MODULE2.21 (BEC_ENABLE_OUT)
BGH1: Q3.4 (G), R1.2
BGH2: Q1.4 (G), R2.2
BGL1: Q4.4 (G), R4.2
BGL2: Q2.4 (G), R3.2
CAN1_LED: IC6.1 (SCIO), MODULE2.33 (CAN1_LED), R10.1, R26.1
CAN1_RX: IC3.4 (RXD), MODULE2.38 (CAN1_RX)
CAN1_TX: IC3.1 (TXD), MODULE2.39 (CAN1_TX)
CAN1_VDD: C5.2, C7.2, C9.2, CON3.1, CON4.1, IC1.4 (OUT)
CAN2_LED: MODULE2.34 (CAN2_LED), R9.1
CAN2_RX: IC4.4 (RXD), MODULE2.36 (CAN2_RX)
CAN2_TX: IC4.1 (TXD), MODULE2.37 (CAN2_TX)
CAN2_VDD: C6.2, C8.2, C10.2, CON5.1, CON6.1, IC2.4 (OUT)
CGH1: Q11.4 (G), R21.2
CGH2: Q9.4 (G), R22.2
CGL1: Q12.4 (G), R24.2
CGL2: Q10.4 (G), R23.2
GAIN_OUT: LED5.C, MODULE2.22 (GAIN_OUT)
GATE_ENABLE_OUT: LED4.A, MODULE2.23 (EN_GATE_OUT)
GND: C3.2, C4.2, C11.2, C12.2, C13.1, C14.1, C15.1, C45.2, CON7.4, CON7.M$0 (GND), CON7.M$1 (GND), CON8.1, CON9.1, D4.1 (C), D7.1 (A), D7.4 (A), IC1.2 (GND), IC2.2 (GND), IC3.2 (GND), IC3.8 (S), IC3.PAD (GND), IC4.2 (GND), IC4.8 (S), IC4.PAD (GND), IC5.3 (GND), IC6.3 (VSS), J1.5 (GND), J1.S1 (SHIELD), J1.S2 (SHIELD), J1.S3 (SHIELD), LED4.C, MODULE2.41 (GND), R7.2, U$1.P$1, U$3.P$1
GNDD: C5.1, C6.1, C7.1, C8.1, C9.1, C10.1, CON3.4, CON3.M$0 (GND), CON3.M$1 (GND), CON4.4, CON4.M$0 (GND), CON4.M$1 (GND), CON5.4, CON5.M$0 (GND), CON5.M$1 (GND), CON6.4, CON6.M$0 (GND), CON6.M$1 (GND), U$1.P$2
GPIO1: CON2.1, D7.6 (COMMON), MODULE2.25 (GPIO1), R8.1
GPIO2: D7.3 (COMMON), MODULE2.24 (GPIO2), R25.1
LED_BLUE: MODULE2.29 (RGB_LED_BLUE), R11.2
LED_GREEN: MODULE2.28 (RGB_LED_GREEN), R12.2
LED_RED: MODULE2.27 (RGB_LED_RED), R13.2
unnamed: J1.3 (D+), R19.2
unnamed: J1.2 (D-), R20.2
unnamed: MODULE2.30, R6.1
unnamed: CON7.1, F1.P$1 (1)
unnamed: C14.2, IC5.1 (VCC), R27.1
unnamed: LED2.C, R10.2
unnamed: LED1.C, R9.2
unnamed: MODULE2.26 (OVERCURRENT_PROTECT_ADJ), R7.1
unnamed: CON7.2, R8.2
unnamed: CON7.3, R25.2
unnamed: CON3.2, CON4.2, IC3.7 (CANH)
unnamed: CON3.3, CON4.3, IC3.6 (CANL)
unnamed: CON8.3, R28.1
unnamed: CON8.2, R29.1
unnamed: CON5.3, CON6.3, IC4.6 (CANL)
unnamed: CON5.2, CON6.2, IC4.7 (CANH)
unnamed: D4.3 (D2), MODULE2.31, R20.1
unnamed: D4.2 (D1), MODULE2.32, R19.1
unnamed: LED3.R, R13.1
unnamed: LED3.G, R12.1
unnamed: LED3.B, R11.1
PGND: C1.-, C2.-, C24.1, C31.1, C32.1, C35.1, C58.1, C62.1, C63.1, C64.1, C66.1, D1.A, D5.A, D6.A, PAD4.1, Q10.1 (S), Q10.2 (S), Q10.3 (S), Q12.1 (S), Q12.2 (S), Q12.3 (S), R5.2, R5.22 (2), R18.2, R18.22 (2), S1.SHELL (SHELLL), U$3.P$2
PHASE_A: MODULE2.2 (PHASE_A), PAD2.1, Q5.1 (S), Q5.2 (S), Q5.3 (S), Q6.5 (D), Q6.6 (D), Q6.7 (D), Q6.8 (D), Q6.P$1 (D), Q7.1 (S), Q7.2 (S), Q7.3 (S), Q8.5 (D), Q8.6 (D), Q8.7 (D), Q8.8 (D), Q8.P$1 (D)
PHASE_A_CURRENT_SHUNT_N: MODULE2.13 (PHASE_A_CURRENT_SHUNT_N), R18.S1
PHASE_A_CURRENT_SHUNT_P: MODULE2.14 (PHASE_A_CURRENT_SHUNT_P), R18.S2
PHASE_A_GATE_HIGH: MODULE2.1 (PHASE_A_GATE_HIGH), R14.1, R15.1
PHASE_A_GATE_LOW: MODULE2.3 (PHASE_A_GATE_LOW), R16.1, R17.1
PHASE_A_GND: MODULE2.4 (PHASE_A_SOURCE_LOW), Q6.1 (S), Q6.2 (S), Q6.3 (S), Q8.1 (S), Q8.2 (S), Q8.3 (S), R18.1, R18.11 (1)
PHASE_B: MODULE2.6 (PHASE_B), PAD1.1, Q1.1 (S), Q1.2 (S), Q1.3 (S), Q2.5 (D), Q2.6 (D), Q2.7 (D), Q2.8 (D), Q2.P$1 (D), Q3.1 (S), Q3.2 (S), Q3.3 (S), Q4.5 (D), Q4.6 (D), Q4.7 (D), Q4.8 (D), Q4.P$1 (D)
PHASE_B_CURRENT_SHUNT_N: MODULE2.15 (PHASE_B_CURRENT_SHUNT_N), R5.S1
PHASE_B_CURRENT_SHUNT_P: MODULE2.16 (PHASE_B_CURRENT_SHUNT_P), R5.S2
PHASE_B_GATE_HIGH: MODULE2.5 (PHASE_B_GATE_HIGH), R1.1, R2.1
PHASE_B_GATE_LOW: MODULE2.7 (PHASE_B_GATE_LOW), R3.1, R4.1
PHASE_B_GND: MODULE2.8 (PHASE_B_SOURCE_LOW), Q2.1 (S), Q2.2 (S), Q2.3 (S), Q4.1 (S), Q4.2 (S), Q4.3 (S), R5.1, R5.11 (1)
PHASE_C: MODULE2.10 (PHASE_C), PAD3.1, Q9.1 (S), Q9.2 (S), Q9.3 (S), Q10.5 (D), Q10.6 (D), Q10.7 (D), Q10.8 (D), Q10.P$1 (D), Q11.1 (S), Q11.2 (S), Q11.3 (S), Q12.5 (D), Q12.6 (D), Q12.7 (D), Q12.8 (D), Q12.P$1 (D)
PHASE_C_GATE_HIGH: MODULE2.9 (PHASE_C_GATE_HIGH), R21.1, R22.1
PHASE_C_GATE_LOW: MODULE2.11 (PHASE_C_GATE_LOW), R23.1, R24.1
PHASE_C_GND: MODULE2.12 (PHASE_C_SOURCE_LOW), S1.IN
TEMPERATURE_SENSOR: C13.2, IC5.2 (OUT), MODULE2.17 (TEMPERATURE_SENSOR)
UART_RX: MODULE2.20 (UART_RX), R29.2
UART_TX: MODULE2.19 (UART_TX), R28.2
USB_VBUS: D2.A, D4.4 (A), J1.1 (VBUS), R6.2
VDC: C1.+, C2.+, C24.2, C31.2, C32.2, C35.2, C58.2, C62.2, C63.2, C64.2, C66.2, D1.C, D5.C, D6.C, MODULE2.42 (VDC), PAD5.1, Q1.5 (D), Q1.6 (D), Q1.7 (D), Q1.8 (D), Q1.P$1 (D), Q3.5 (D), Q3.6 (D), Q3.7 (D), Q3.8 (D), Q3.P$1 (D), Q5.5 (D), Q5.6 (D), Q5.7 (D), Q5.8 (D), Q5.P$1 (D), Q7.5 (D), Q7.6 (D), Q7.7 (D), Q7.8 (D), Q7.P$1 (D), Q9.5 (D), Q9.6 (D), Q9.7 (D), Q9.8 (D), Q9.P$1 (D), Q11.5 (D), Q11.6 (D), Q11.7 (D), Q11.8 (D), Q11.P$1 (D)
VDD_5V: C3.1, C4.1, C11.1, C12.1, C15.2, C45.1, CON8.4, D2.C, D7.2 (C), D7.5 (C), F1.P$2 (2), IC1.3 (IN), IC2.3 (IN), IC3.3 (VCC), IC3.5 (VIO), IC4.3 (VCC), IC4.5 (VIO), IC6.2 (VCC), LED1.A, LED2.A, LED3.+ (A), LED5.A, MODULE2.40 (5V_OUT), R26.2, R27.2

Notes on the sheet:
PHASE_B
PHASE_A
PHASE_C
UAVCAN
INDICATION
A bulk capacitor is required (not shown on this schematic). Its exact capacitance depends on the maximum power rating of the device.
Capacitor battery
These capacitors should be placed as close as possible to the power transistors.
Temperature sensor
Battery connection
The minimum specific bulk capacitance is 20 μF/A (e.g. an ESC rated for 20 A DC requires at least 400 μF).
Place ground and power ground junction as close to negative supply pad as possible
LOW SIDE INTERFACES
HIGH SIDE INTERFACES
In case CAN2 is not used leave pins CAN2_TX CAN2_RX floating.
In case POWER_ENABLE_IN is not used, leave it floating.
Place close to power mosfets
AUX
Power should be connected with multi-strand 12AWG wire in silicone insulation
PCB hole diameters for wires are based on the chart from PCBLibraries.com http://www.pcblibraries.com/downloads/temp/ANSI_Wire_Gauge_Charts_6433393.pdf

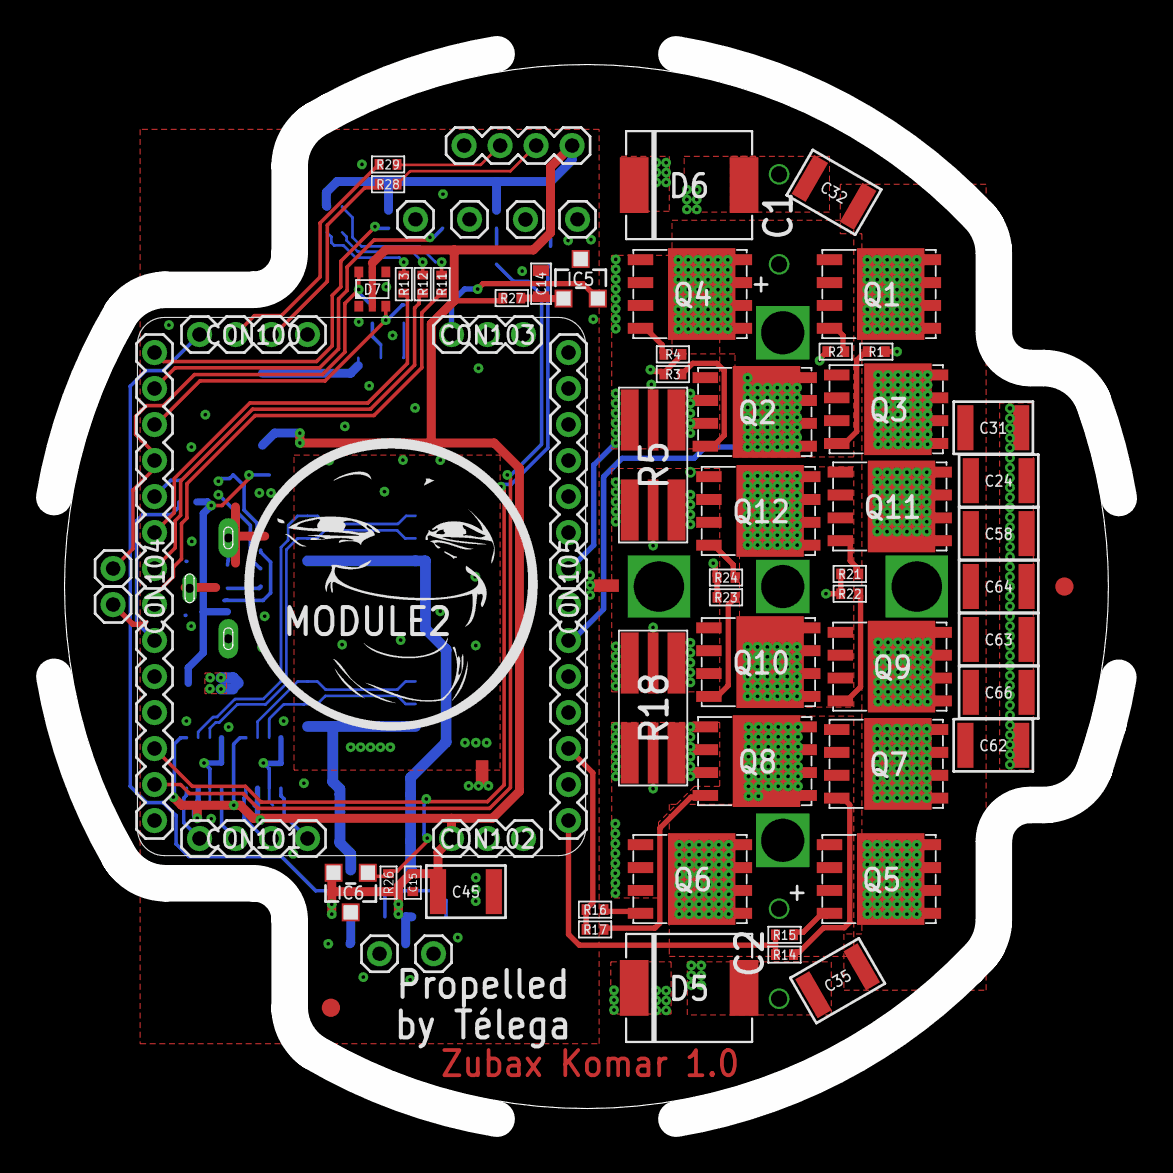
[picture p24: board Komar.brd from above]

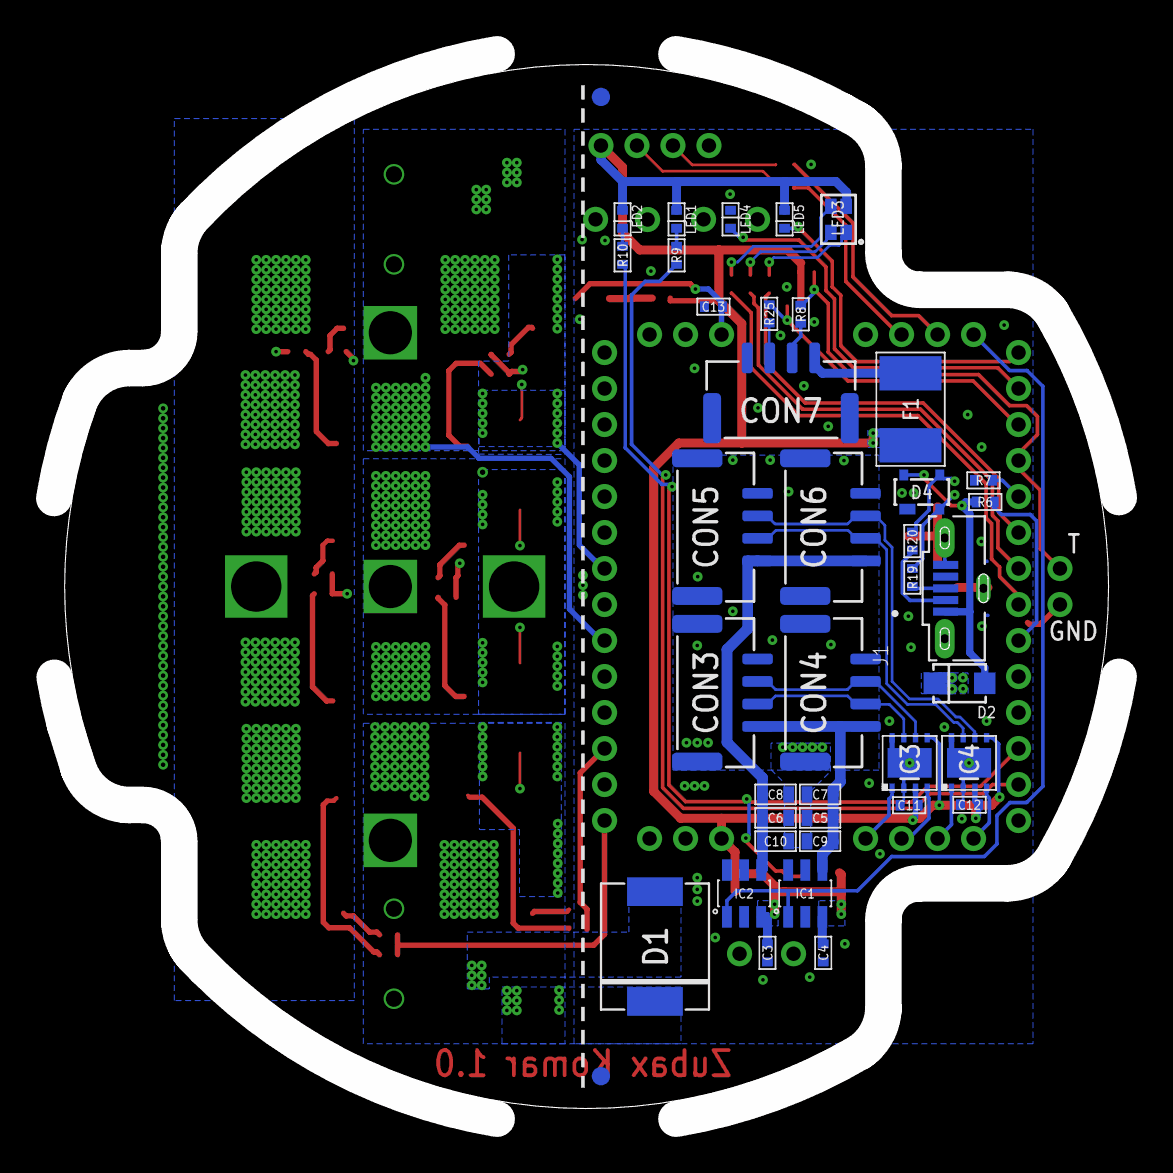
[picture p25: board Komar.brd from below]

Board: 4 copper layers, 59.2 x 59.2 mm, 113 parts (40 on the bottom side), 74 nets.

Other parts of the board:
U$2: YOBA_17X17

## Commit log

2018-11-06 V0.1 import
    [BOM.xls, OpenMyxa.brd, OpenMyxa.sch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]
2018-11-06 V0.2 import
    [OpenMyxa.brd, OpenMyxa.sch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]
2018-11-10 minor poly update
    [OpenMyxa.brd]
2019-01-08 minor updates
    [OpenMyxa.brd]
2019-04-09 aluminum enclosure
    [bottom_enclosure.SLDPRT, cover.SLDPRT, top_enclosure.SLDPRT]
2019-04-10 Connectors color fix
    [OpenMyxa.brd, OpenMyxa.sch]
2019-05-04 reverse model import from fusion
    [bottom_enclosure.SLDPRT, top_enclosure.SLDPRT]
2020-01-06 Migration to updated mitochondrik library
    [OpenMyxa.brd, OpenMyxa.sch]
2020-05-05 component selection updates
    [OpenMyxa.brd, OpenMyxa.sch]
2020-05-06 TVS diode updated
    [Komar.brd, Komar.sch]
2020-05-07 Massive attributes update
    [Komar.brd, Komar.sch]
2020-05-08 Single wire memory for power stage descriptor storage added
    [Komar.brd, Komar.sch]
2020-05-08 MOSFETs replacement
    [Komar.brd, Komar.sch]
2020-05-08 Minor silkscreen updates
    [Komar.brd, Komar.sch]
2020-05-08 attribute updates
    [Komar.brd, Komar.sch]
2020-05-11 CAN transciever replaced due for logistic reasons
    [Komar.brd, Komar.sch]
2020-05-11 NETs naming updates
    [Komar.brd, Komar.sch]
2020-05-12 powerstage rerouting partially completed
    [Komar.brd, Komar.sch]
2020-05-12 Routing completed
    [Komar.brd, Komar.sch]
2020-05-12 minor tweaks
    [Komar.brd]
2020-05-12 libraries cleanup
    [Komar.brd, Komar.sch]
2020-05-12 Minor library cleanup
    [Komar.brd, Komar.sch]
2020-05-12 minor attribute updates
    [Komar.brd, Komar.sch]
2020-05-12 C32, C35 marked as DNM
    [Komar.brd, Komar.sch]
2020-05-12 CAN transcievers rerouting
    [Komar.brd, Komar.sch]
2020-05-12 Redundant thermistor pads removed
    [Komar.brd, Komar.sch]
2020-05-12 width updates
    [Komar.brd]
2020-05-13 minor attribute extension
    [Komar.brd, Komar.sch]
2020-05-13 CAN LEDs moved to other LEDs.
    - DCP connector replaced with PLS-2 connector (marked DNM anyway)
    - All LEDs moved 2 mm up
    [Komar.brd, Komar.sch]
2020-05-13 Pins for lightpipes and capacitor support elements added
    [Komar.brd, Komar.sch]
2020-05-13 minor via adjustments
    [Komar.brd]
2020-05-13 DRC violation fix
    [Komar.brd]
2020-05-14 Holes diamters for wires increased to fit AWG 14 and AWG 12 wires
    [Komar.brd, Komar.sch]
2020-05-14 Phase wires holes diameter further increased
    [Komar.brd, Komar.sch]
2020-05-15 silkscreen update
    [Komar.brd, Komar.sch]
2020-05-15 minor attribute update
    [Komar.brd, Komar.sch]
2020-06-02 LED1, LED2 attribute update
    [Komar.brd, Komar.sch]
2020-06-05 Create Komar housing.f3d
2020-06-06 minor schematic graphics corrections
    [Komar.sch]
2020-06-10 Update Komar.brd
    It is now Komar 1.0
    [Komar.brd]
2020-06-10 manufacturing instruction update
    [Komar.sch]
2020-06-16 assembly BOM table updated
2020-07-08 manufacturing guide for phase connector
2020-07-08 Solder mask update
    [Komar.brd]
2020-07-09 Rigit phase connector docs
2020-07-10 assembly video had to go
2020-07-11 More detailed assembly instructions
2020-07-11 Fix the BOM by removing the forgotten protection cap screws, harmonize the description with the BOM
2020-07-13 Remove the screws properly, for good.
2020-08-29 Panel template update.
    [Komar.brd, Panel_template.brd]
2020-08-31 Panel design rules update
    [Panel_template.brd]
2020-09-17 Update Komar housing.f3d
2021-01-08 Manufacturing update (#18)
    * Create PCB SPACER.brd
    * pictures update
    * Update readme.md
    * Update readme.md
    * Update readme.md
    * Update readme.md
    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
    [PCB SPACER.brd]
2021-01-08 Revert "Manufacturing update (#18)" (#19)
    This reverts commit 5132449b39217a135044f1e9cd234c0103d1caa6.
    [PCB SPACER.brd]
2021-01-09 Manufacturing update (#20)
    * 3d printed plastic PCB spacer replaced with single PCB spacer.
    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
    [pcb spacer.brd]
2021-03-19 Rigid phase connector assembly instruction (#22)
    * pics import
    * Update rigid_phase_connector.md
    * Create rigid phase connector jig.f3z
    * Update rigid_phase_connector.md
    * Pictures update
    * Update rigid phase connector jig.f3z
    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
    [rigid phase connector jig.f3z]
2021-07-29 changed usb back to through-hole (#27)
    * changed usb back to through-hole
    * fixes 42
    * Updated changelog fixes #26
    * minor changes to fixes #26
    * changes related to #26
    * updated power via connection
    * usb power via minor routing update
    * usb footprint changed, fix usb vbus trace width
    [Komar.brd, Komar.sch]
2021-07-31 erc warnings are acknoledged
    [Komar.brd, Komar.sch]
2021-08-01 Revert "erc warnings are acknoledged"
    This reverts commit bd3fd96e0683a0248e85c5e03ae5492be1d8f03c.
    [Komar.brd, Komar.sch]
2021-08-03 erc warnings are acknoledged (#29)
    (cherry picked from commit bd3fd96e0683a0248e85c5e03ae5492be1d8f03c)
    [Komar.brd, Komar.sch]
2022-11-28 added alternative parts (#34)
    * added alternative parts
    schematic update
    README update
    also repacked the manufacturing docs
    * Fixed README table
    fixed README table format
    * added proper attributes to Micro USB - J1
    can't remove the pre-existing attributes so I just added.
    * removed unnecessary attributes
    * Removed unnecessary attributes
    * added line regarding Micro USB fix
    * Updated README
    added function column
    * Update README.md
    [Komar.brd, Komar.sch]
2022-11-28 Updated README
    changed Komar DC/Battery wire from 2.5mm to 12 AWG
2022-11-28 Update README (#38)
    changed DC/Battery power wire to 12 AWG from 2.5mm
2023-01-06 Increase the hardware over-current protection limit; remove incorrect alternative part number (#40)
    * changed R7
    changed R7 from ERJ-2RKF1501X to ERJ-PA2F1602X
    * updated changelog
    * adding remove alternative to this pull request (#43)
    * removed alternative from schematic & updated changelog
    * added v1.4
    reverted changes
    added v1.4 - removed alternative of BAV99HDWQ-13
    [Komar.brd, Komar.sch]
2023-01-24 updated thermistor alternative (#45)
    * changed alternative to correct part number
    changed MCP9701T-E/TT to MCP9700T-E/TT
    * Added to changelog
    [Komar.brd, Komar.sch]
2023-05-10 Add VSI config (#47)
    * added default VSI configuration
    * added clarification
    clarified that VSI configuration only applies to Komars with Telega v1.0
    * Remove the DC voltage gain from the VSI config
    This is actually supposed to be configured correctly by default; see https://github.com/Zubax/telega/issues/594
    ---------
2023-07-03 Cosmetic upgrades (#48)
    Fix #46
    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
    [Komar.brd, Komar.sch]
2024-01-10 Added power wires length (#51)
